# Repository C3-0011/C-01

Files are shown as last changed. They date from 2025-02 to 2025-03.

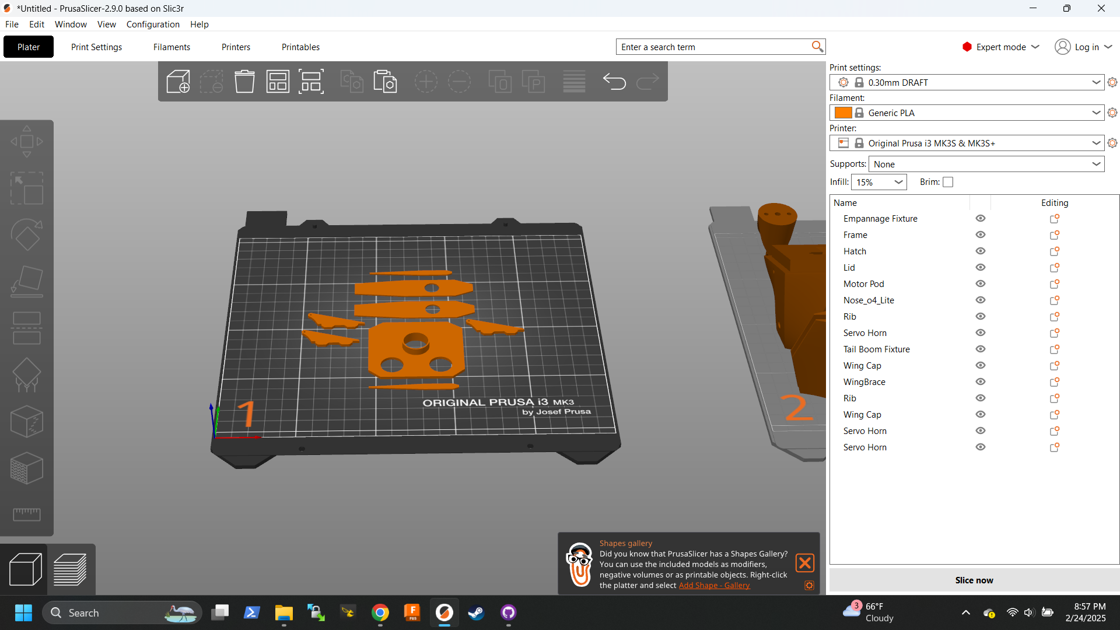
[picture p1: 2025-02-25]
Images/Flat Parts.png

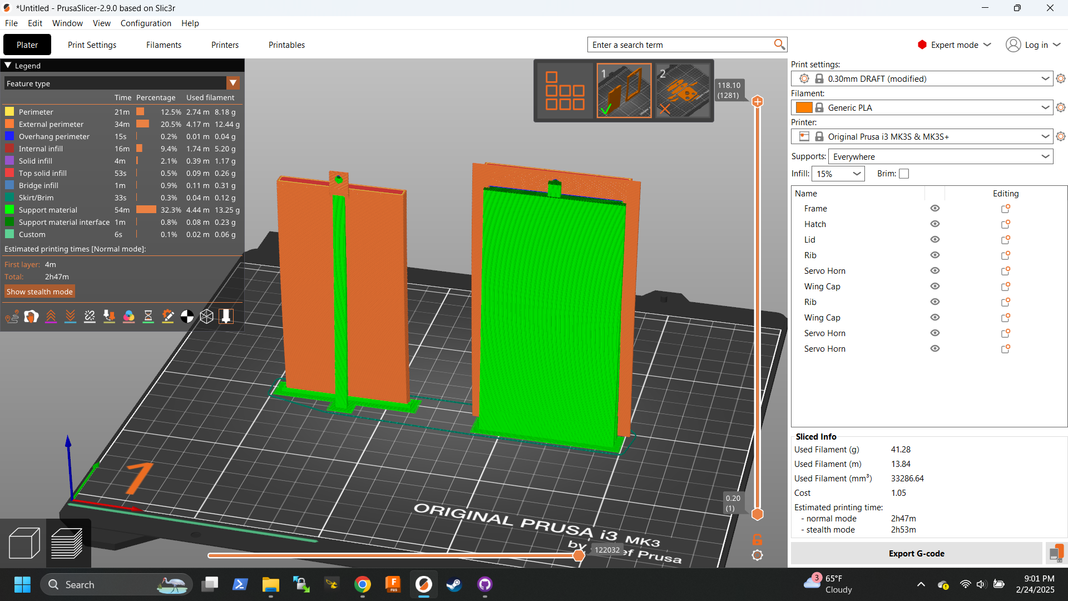
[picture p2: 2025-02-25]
Images/Hatch Parts.png

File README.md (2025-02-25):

# C-01
 T-1 Ranger clone made from foamboard and 3D printed parts

Screenshot (29)

### Parts List:
| Qty | Part | 
| --- | --- |
| 2 | ~2450kv Motors |
| 2 | 5in tri-blade or 6in bi-blade propellers |
| 2 | ~40A PWM Escs |
| 3 | 9g Servo Motors |
| 1 | 360mm X 16mm X 1mm Carbon Fiber Tube |
| 1 | 500mm X 10mm X 1mm Carbon Fiber Tube |
| 1 | 5+ Channel PWM Reciever |
| - | Servo Extensions |
| - | Pushrods |
| - | Video System |
| - | BEC |

## Print Instructions
All of the 3D printed parts are printed in PLA. Lightweight PLA may be suitable but has not been tested.
Print settings are:
- 0.3mm Layer Height
- Cubic 10% Infill
- No supports
Unless stated otherwise.

### Flat Components
Flat Parts
Print the following number of each flat part in the orientation shown above:
| Number | Part |
| --- | --- |
| 2 | Rib |
| 3 | Servo Horn |
| 2 | Wing Cap |
| 1 | Frame |

### Fixtures
Fixtures
Print the following number of each fixture component in the orientation shown above
| Number | Part |
| --- | --- |
| 2 | Wing Brace |
| 2 | Motor Pod |
| 1 | Tail Boom Fixture |
| 1 | Empannage Fixture |

### Hatch Components
Hatch Parts
Print one of each Hatch and Lid components in the orientation shown above. This requires support material on the Hatch component as a minimum, and the Lid also benefits from the stability of adding support. A raft or brim, or slower print speed may help if the Lid component is struggling to adhere to the bed. After printing, install the M3 threaded insert / nut into the 5mm hole in the hatch component using a soldering iron.

### Nose
Nose
Print the nose in the orientation shown above, with the front face flat on the build plate.

If you are using the Analog 22mm nose or the Vista nose, supports should not be required. If you are using the O4 Lite nose then supports are needed, but only to support the USB port. Place a support enforcer such that it covers the "top" part of the usb hole that will need support. You could also enable support everywhere and spend time picking it out, or disable supports completely and file away any sag that may have occured.
o4 Nose

## Cutting Foam Parts
The foam parts are all made from generic Readi-Board from the dollar store. Science fair foam board is not suitable for this model, as it is too dense. The PDF plans are designed to tile and be taped together to form patterns that can be adhered to the stock foamboard with temporary glue, then cut out with a hobby knife. There are 4 sets of patterns, HS (Horizontal Stab.), sides, and tops all have 3 sheets, and the wings pattern has 10 sheets. The wings pattern is made from 2 rows of 5 sheets, with the numbering starting in the top left, going left to right, then repeating on the lower row. The vertical stabilizer pattern is small enough to be printed on one sheet.

I reccomend you calibrate your printer using the 35mm square on the sides3 pdf. To do this, print sides3 at a scale of 100% (never scale to fit) and measure the square with calipers. Then when you print the patterns set the scale equal to: 100 * (35 / your measurement). While cutting out the parts, only cut the very outline for now. The assembly section will give instructions on what to do with the other lines.

 ## Assembly
 The assembly goes much like most Flite Test aircraft, start by building the wings first, then assemble the empennage, then integrate everything as you finish with the fuselage.

 ### Wings
 The wings of the C-01 are inspired by the wings of the FT-3D, I highly encourage you to watch the wings section of the FT-3D build video to see how to score and bevel the lines marked in the wing. Before starting, cut the gray sliver that crosses the leading edge out of the wing, this is where the motor pod will attach. The assembly of the C-01 wings is almost identical to this video, apart from using 3D printed forms to give the wing its shape instead of using foam and the spar. First score the fold lines, and double-bevele the leading edge, and single bevel the aileron on the control surface side. Then glue the Rib component at the root of the wing such that it will force the wing to take the airfoil shape, then do the same with the Wing Cap component at the wingtip. Now follow the gluing and folding procedure in the FT-3D video, but skip the steps where Josh glues down the strips of foam and installs the spar, the C-01 spar goes in at final assembly. Inserting (but not gluing) the motor pod may help ensure the wing takes the proper shape. Make sure to hold, clamp, or press the wing into shape while the hot glue cools. Take the motor pod out if you inserted it. After the wing is cool, attach the motor to the motor pod, then clear any excess glue away from the slot where the motor pod will go. Test fit the motor pod, both pods are identical, but they have a right side up that is flipped for opposite wings. The pod should sit flush against the wing on both sides, and face forward. Note that because the wings are swept, this has the effect of making it look like the motor is pointing towards the wing root before it is attached to the aircraft. If the motor pod is pointing towards the wingtip, it is on backwards. This is also a good time to ensure the motor wires are pointing in a good direction. Once you are sure the motor pod is set up right, insert the motor pod slightly to keep glue from getting on the half-circle where it will touch the wing spar (this is here to help keep the aircraft square during final assembly) then apply a generous amount of glue anywhere the pod will contact the foam. Clean the excess glue off before it cools. Finally glue the Wing Brace component to the root of the wing, such that its rearmost part lies on the hinge axis. This part will bridge the gap between the wing and the fuselage. Repeat these steps for the other wing. When finished, it should look like this: 








### Empennage

Push the Empennage Fixture onto one end of the 16mm carbon fiber tube, pushing it all the way until it is flush. Score and bevel the elevator hinge, beveling on the control surface side, 40mm from the trailing edge of the horizontal stabilizer. Clean the slots in the empennage fixture that the stabilizers will fit into. First push the horizontal stabilizer into place, then the vertical stabilizer. Some CA glue can be used to secure the stabilizers to the fixture, and the fixture to the carbon fiber tube. Cut a space into the vertical stabilizer for the elevator servo, and install a 9g servo there. This is a good time to create and attach the linkages. Use one of the 3D printed servo horns on the elevator. Make sure that the hole in the servo horn is directly above the hinge line when it is glued in place and in the neutral position. You can feed the servo wire through the carbon fiber tube with an extension.

Next install the Tail Boom Fixture onto the other end of the carbon fiber tube. This fixture will sit 63mm from the fuselage end of the tube. Note that this piece is taller than it is wide, and needs to be attached as such. Ensure that it is 63mm from the end of the tube with the "pointy" end facing the empennage, and that it is square with the tail surfaces, then glue it in place with some CA. It should look like this now:



### Final Assembly
First install your video system into your nose of choice. Then take your top and bottom pieces, and remove the paper from one side of them. Next using your calipers score a line 4.4mm from the sides of the top and bottom pieces along the exposed foam. Cut along this line to (but not through) the bottom paper, then remove the piece of foam, these will form a "B" style assembly in the finished fuselage. Next glue the frame piece onto the forward end of the tail boom, making sure it is square (the holes will go up and the "bottom" of the 3d print will be flush with the end of the tube). Then glue the tail boom assembly to the "Bottom" foam piece, applying hot glue under the tail boom fixture and frame pieces. It may be helpful to preform the foam before every step so it takes the bendy shape easily. Next glue the nose piece onto the bottom foam piece, it will sit flush with the bottom as the piece of the nose slots on/over the bottom piece. Next cut the 10mm holes out of the side pieces. Then remove the paper from the inside back section of the side pieces and preform them to the shape they need to take. Add lots of glue along one side of the paper on the edge of the bottom piece, and the side of the nose, frame, and tail boom fixture pieces, and push the corresponding side foam piece onto the bottom piece, forming both the side and bottom to take eachother's shape as the glue cools, then repeat this on the other side. Next tack the 10mm carbon tube in place inside the spar holes, centered over the airframe. Next grab one wing. Test fit the wing, ensuring that the spar does not snag as it is inserted. You should feel how it locates onto the half-circle on the end of the motor pod. Once you are sure the fit is good, apply a generous amount of hot glue onto anywhere the wing will contact the fuselage, and push it firmly against the fuselage. While the glue dries, make sure the wing is parallel to the tail boom. The C-01 has a designed angle of incidence of zero, and the wings are coplanar with the tail boom to make alignment by eye easier. Repeat this with the other wing. Once both wings are installed, install the aileron servos forward of the "Frame" piece. This will involve cutting a hole for them in the fuselage sides underneath the wings. Then install the servo horns and linkages. Then install the reciever behind the wing spar, and put together and test the electrical system. Once the top is on it will be very difficult to access this area, so ensure everything is working properly before moving forward. When you are ready to put the top on, add glue everywhere it will contact the fuselage, and press it into place. Next cut a 58mmx117mm hole in the top plate, with the front edge of the hole 13mm from where the top plate meets the nose piece. Glue the Hatch piece into this hole, and add fuzzy velcro to the space beneath it to secure a battery.

I will add photos here when I rebuild my fuselage this week.

## Misc

The C-01 is designed to be flown with the motors on seperate channels for differential thrust, and the aileron servos on independent channels so that flaperons can be configured. Give the control surfaces roughly 30 degrees of deflection, and I'd reccomend 20-30 percent expo. I fly my C-01 with a 3s 2200, however with the the speced motors, props, and escs, it should be capable of 4s without burning any electronics. Balance the C-01 roughly over the spar.

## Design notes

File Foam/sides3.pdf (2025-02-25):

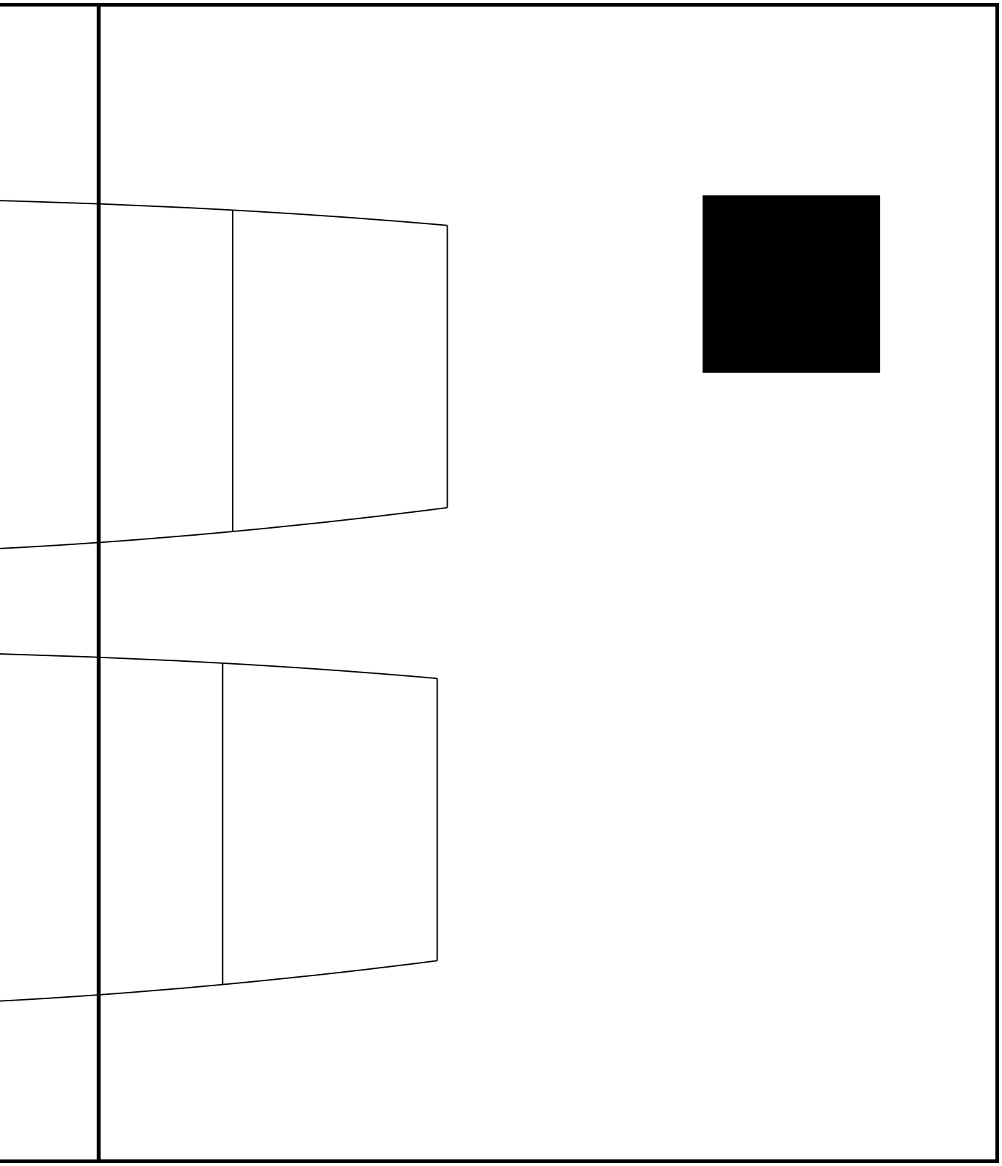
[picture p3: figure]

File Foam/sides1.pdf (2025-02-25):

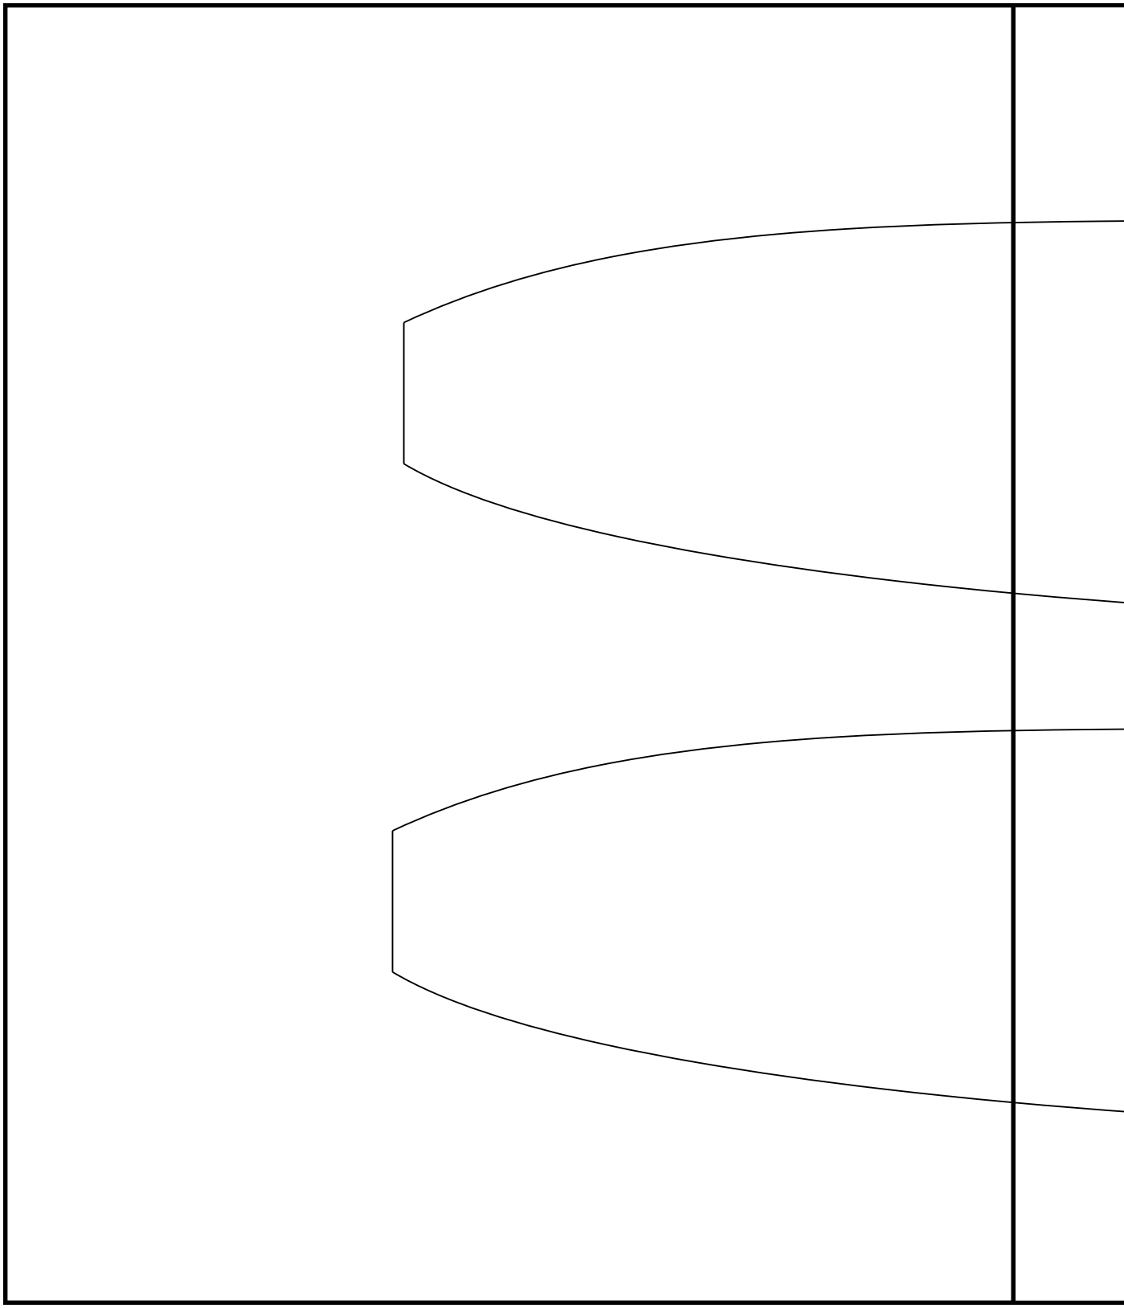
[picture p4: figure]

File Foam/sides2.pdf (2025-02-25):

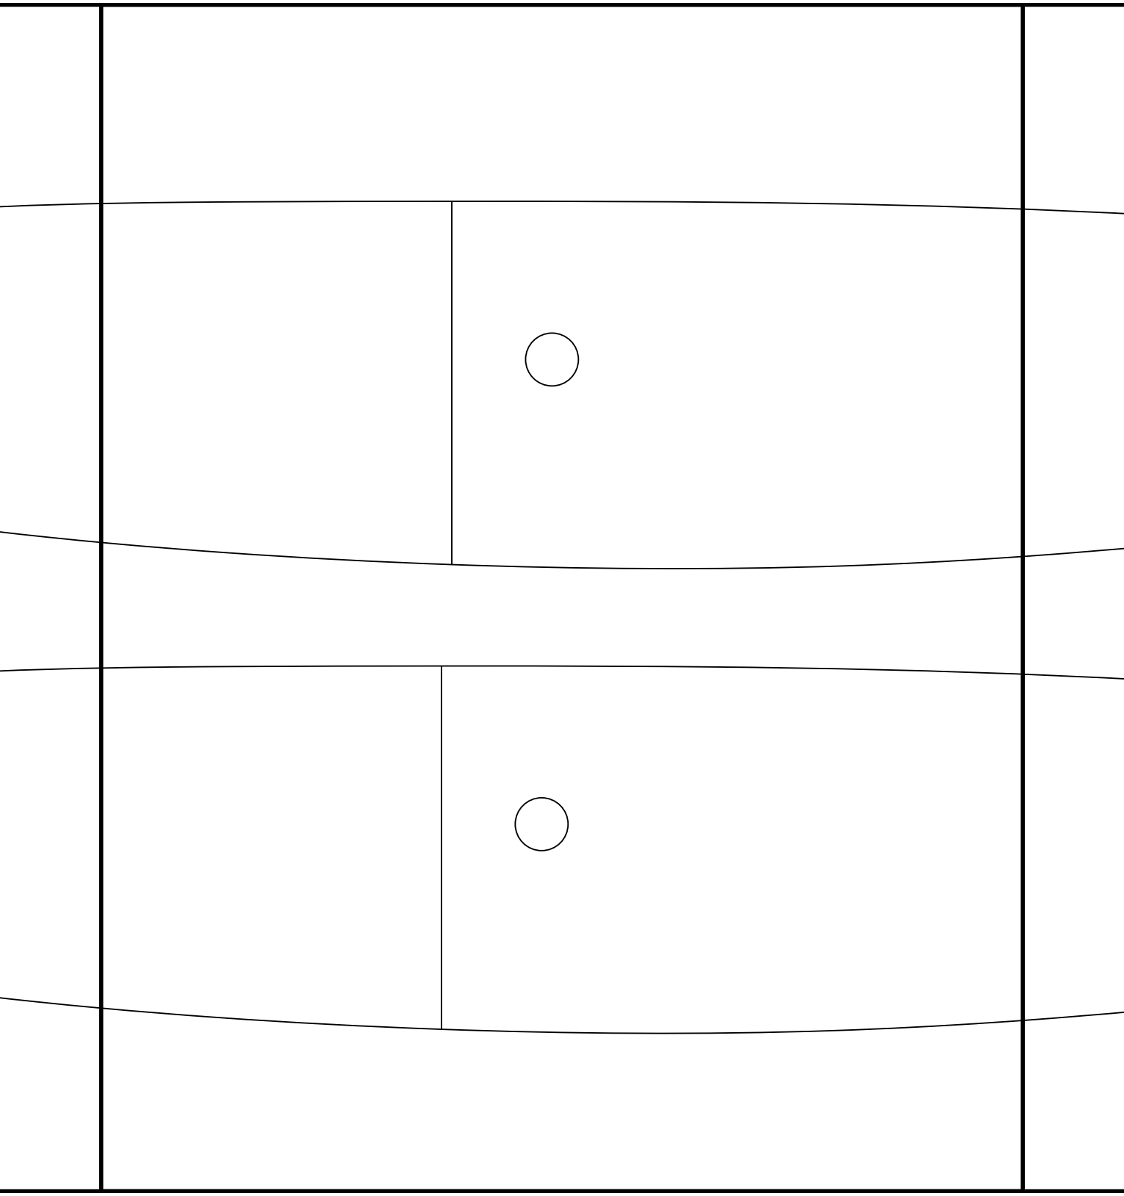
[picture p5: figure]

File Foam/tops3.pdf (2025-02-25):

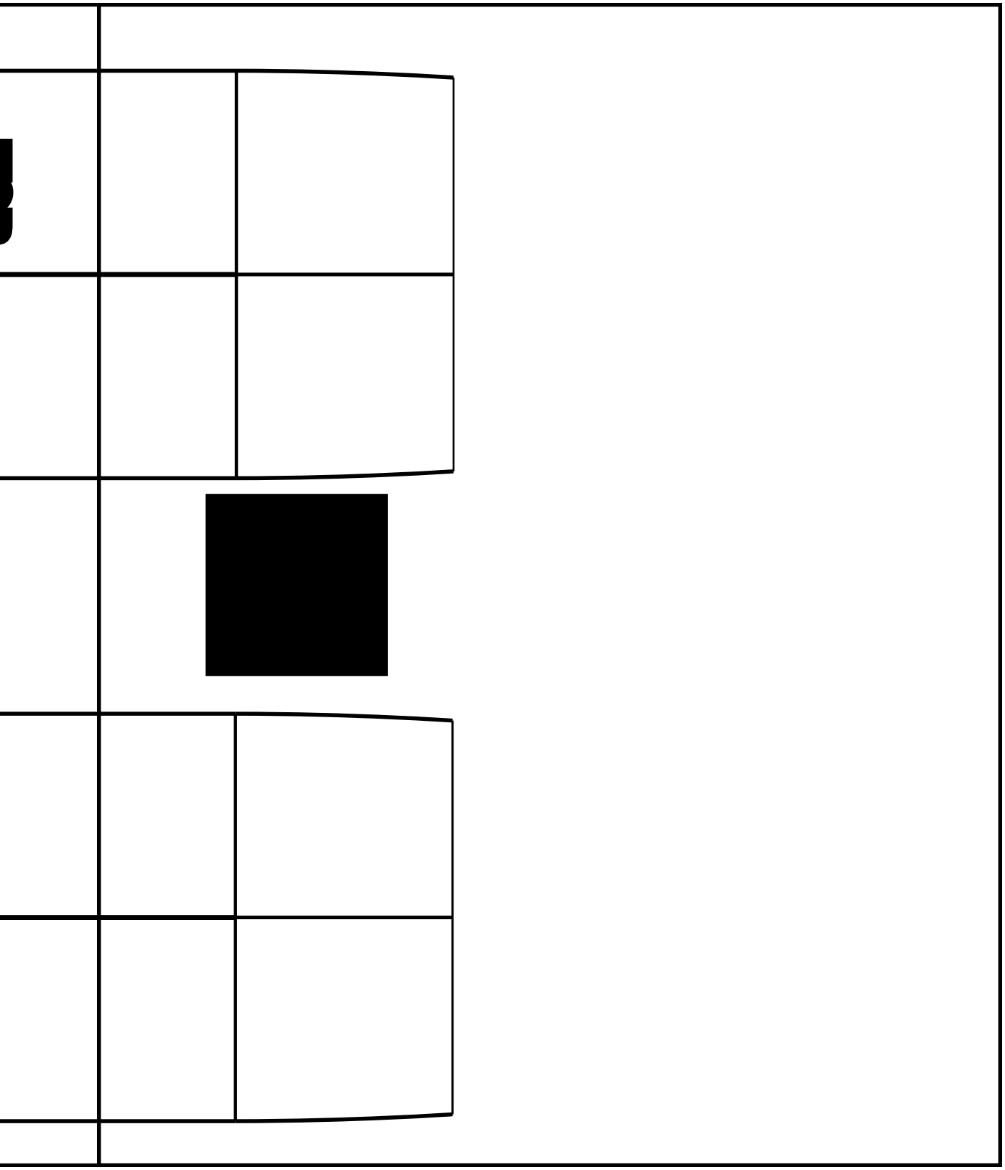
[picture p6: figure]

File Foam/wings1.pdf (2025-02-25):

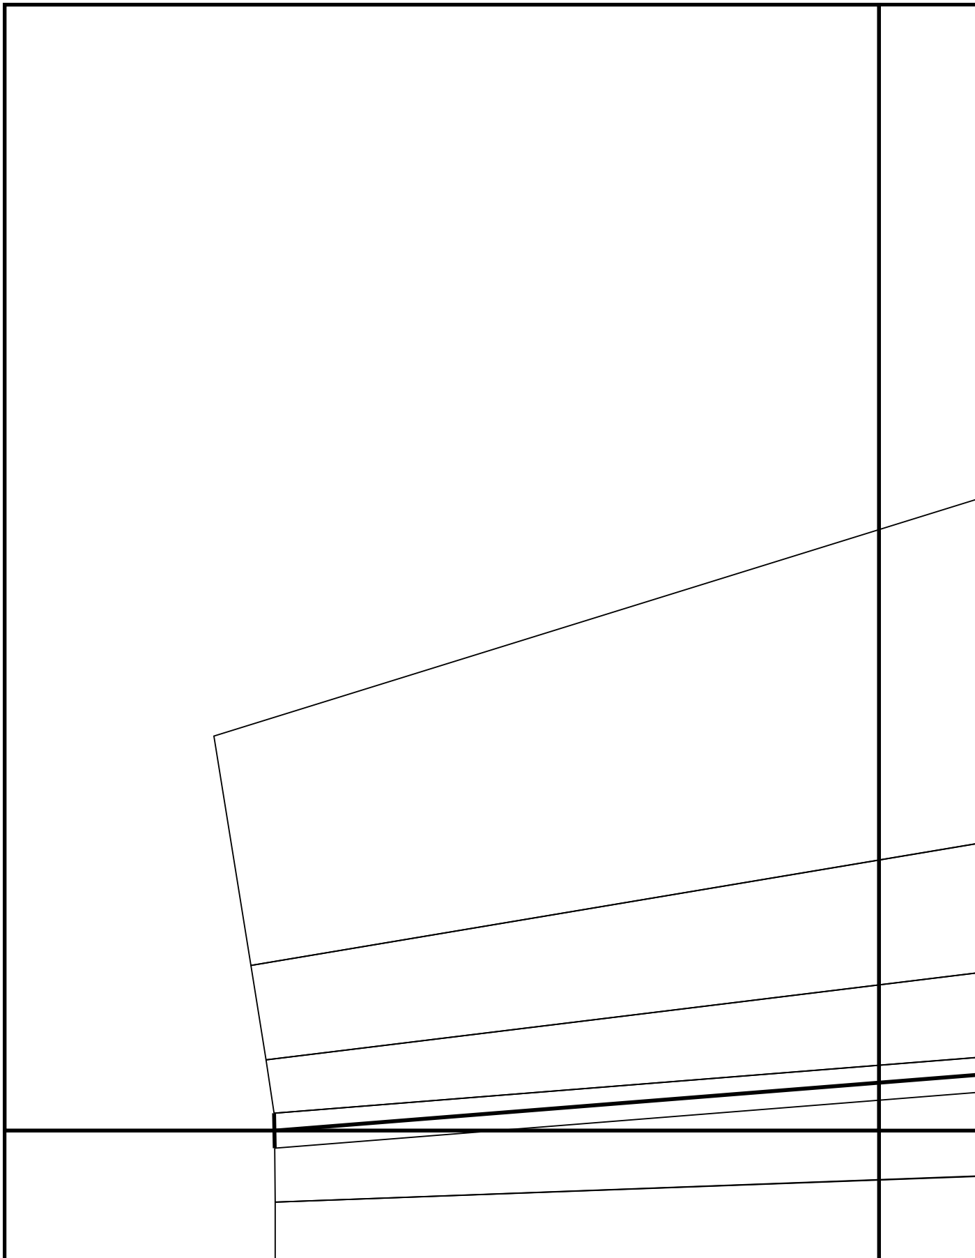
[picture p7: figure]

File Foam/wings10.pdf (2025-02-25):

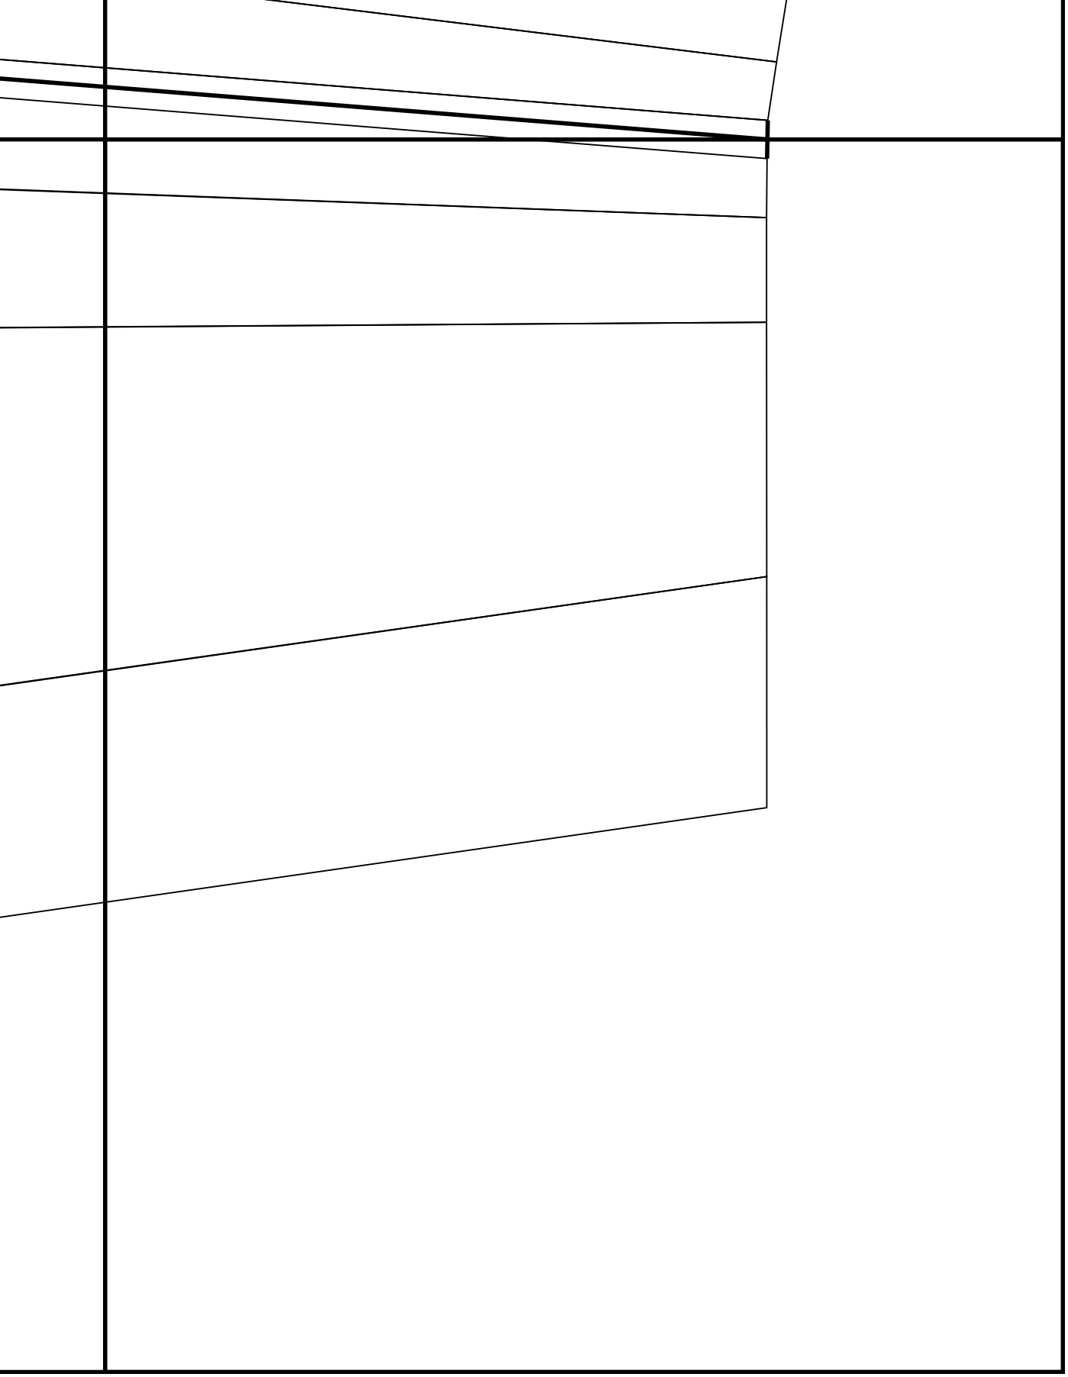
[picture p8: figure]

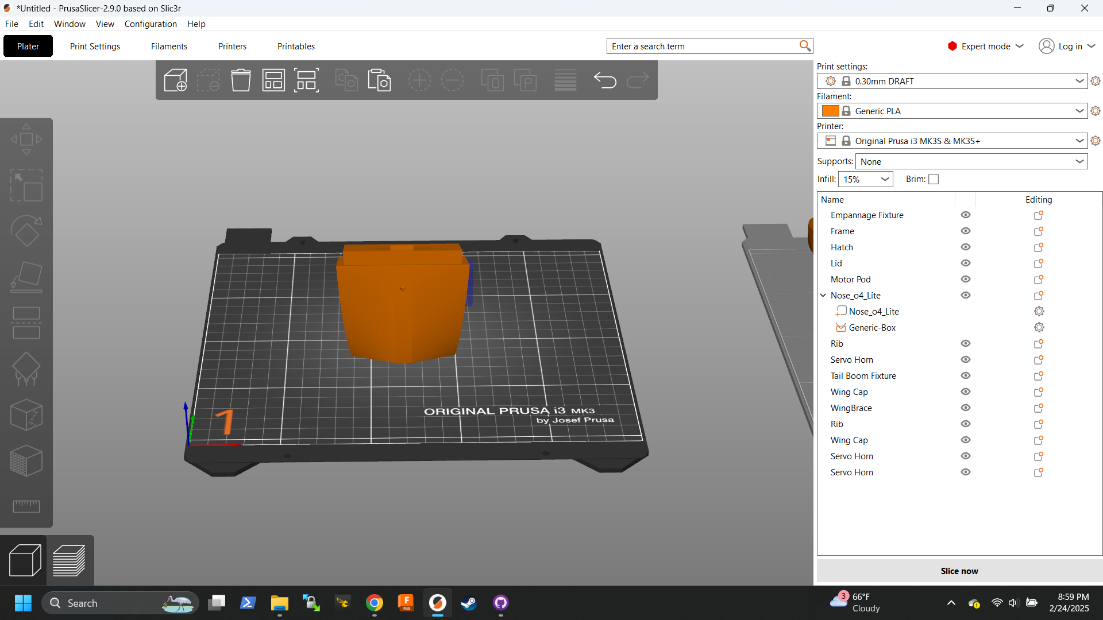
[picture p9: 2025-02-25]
Images/Nose.png

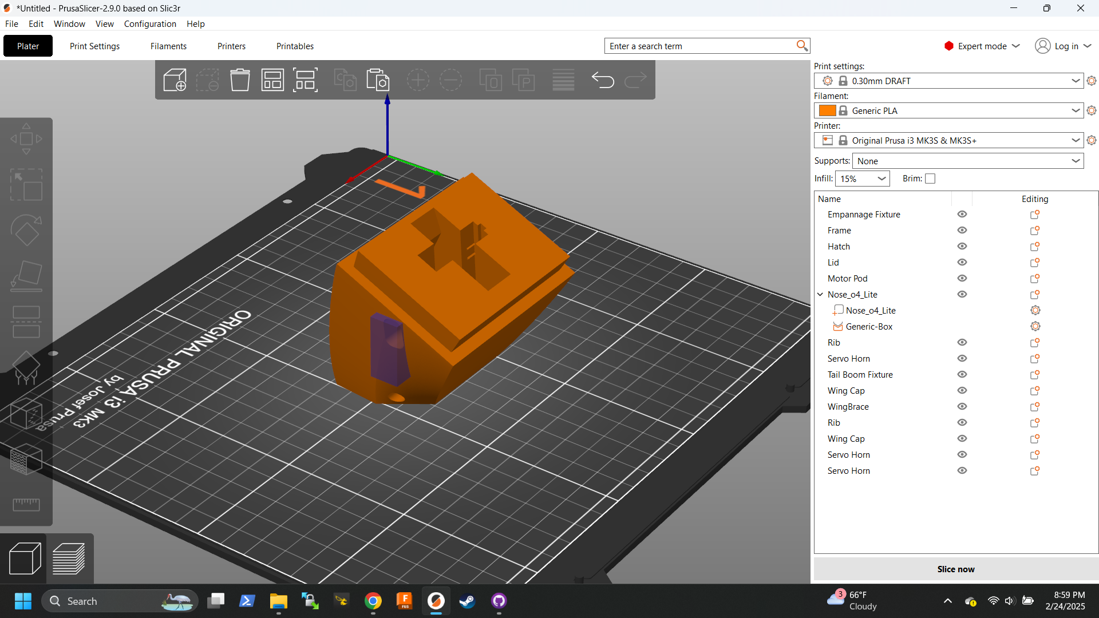
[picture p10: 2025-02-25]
Images/o4 Nose.png

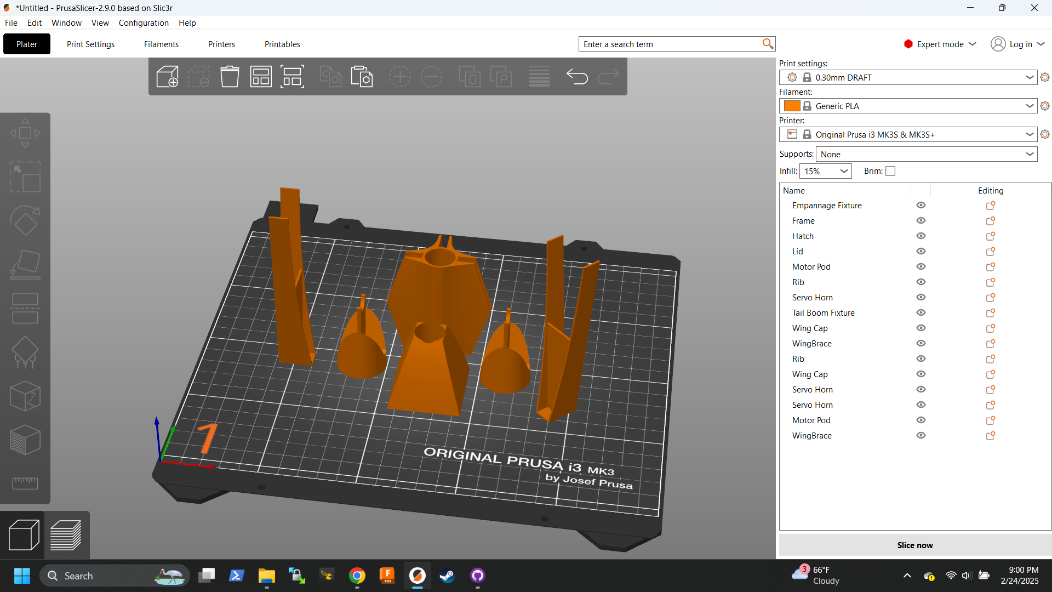
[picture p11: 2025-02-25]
Images/Fixtures.png

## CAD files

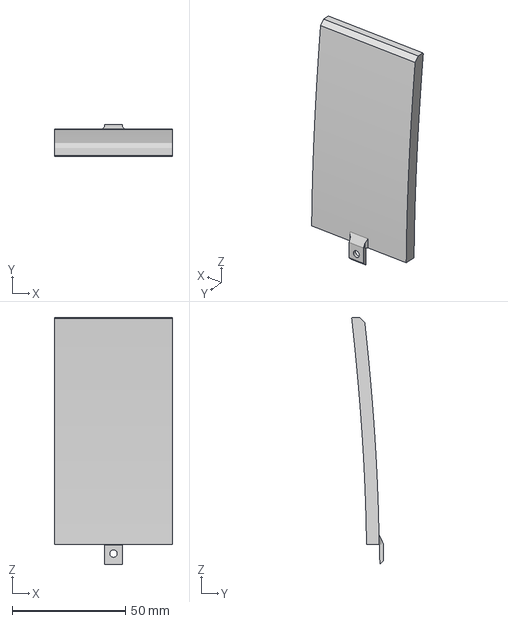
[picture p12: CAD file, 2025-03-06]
PLA/Lid.3mf
52.4 x 14.0 x 109.3 mm

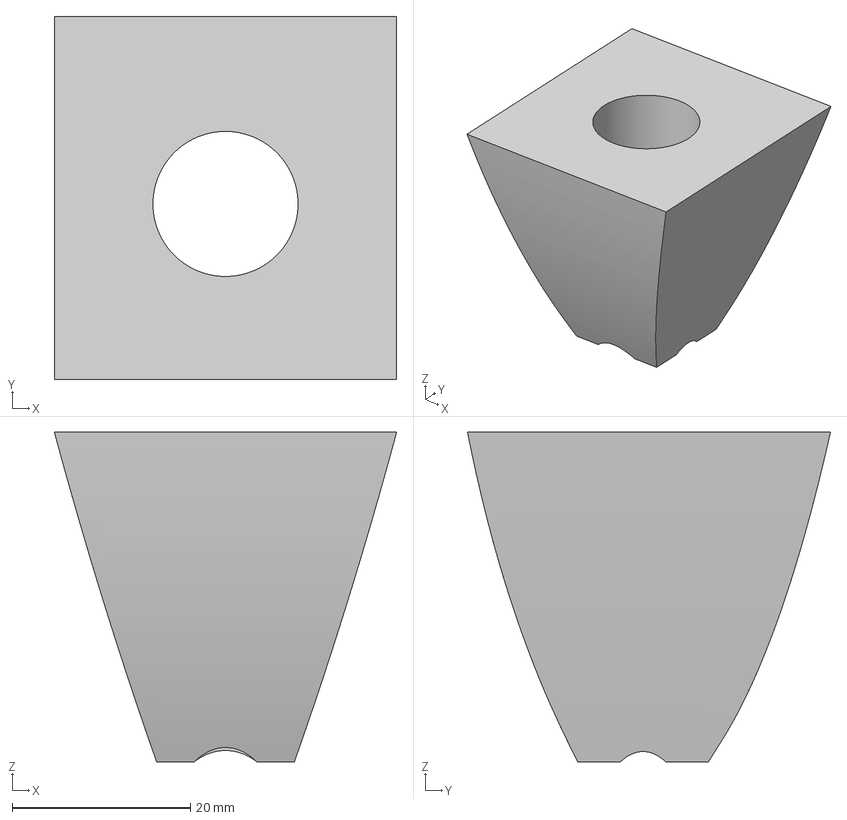
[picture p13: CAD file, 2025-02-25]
PLA/Tail Boom Fixture.3mf
38.4 x 40.8 x 37.0 mm

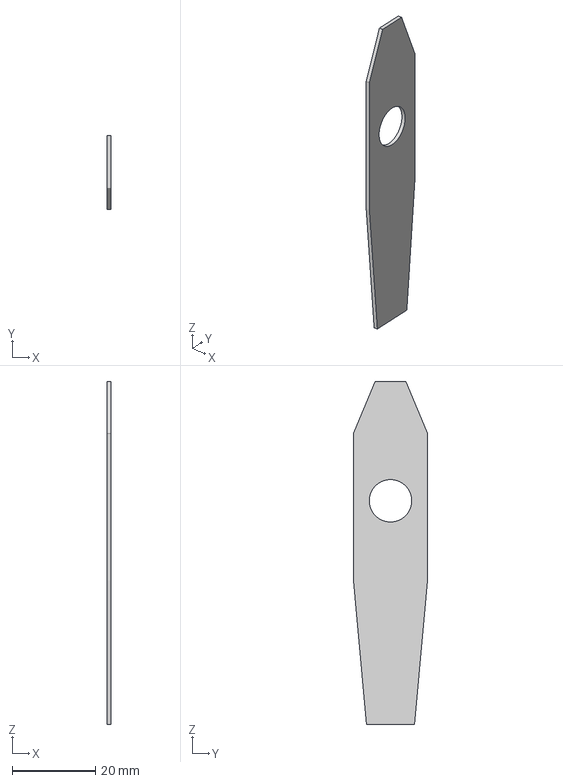
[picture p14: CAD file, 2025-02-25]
PLA/Rib.3mf
1.00 x 17.8 x 82.6 mm

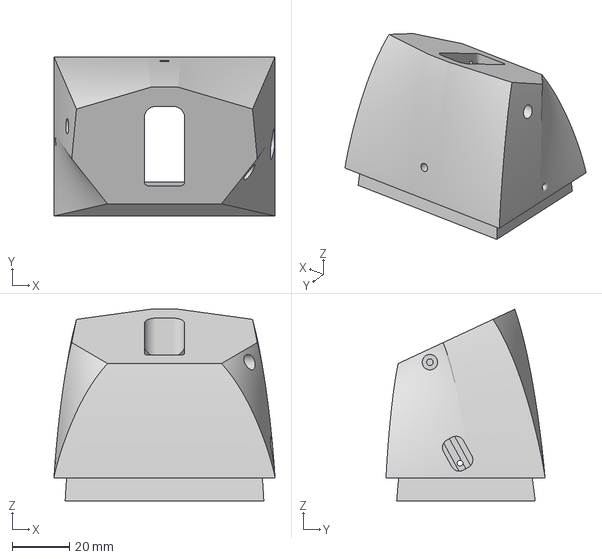
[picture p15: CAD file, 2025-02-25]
PLA/Nose_o4_Lite.3mf
77.3 x 55.6 x 67.0 mm

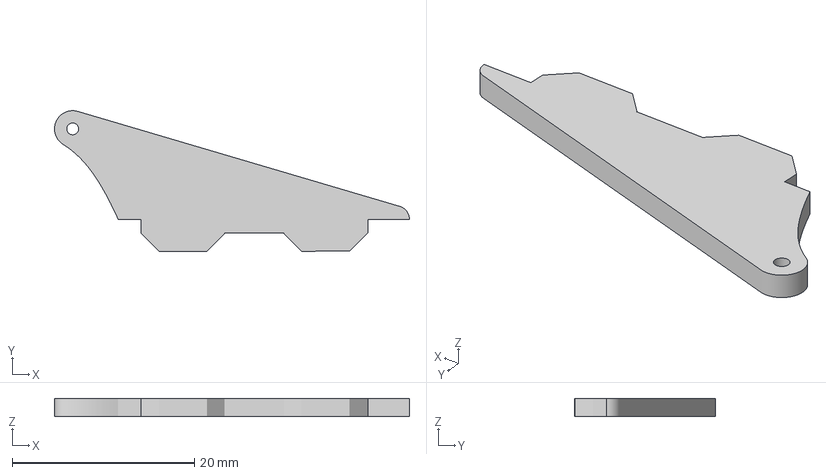
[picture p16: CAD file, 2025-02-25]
PLA/Servo Horn.3mf
39.0 x 15.5 x 2.00 mm

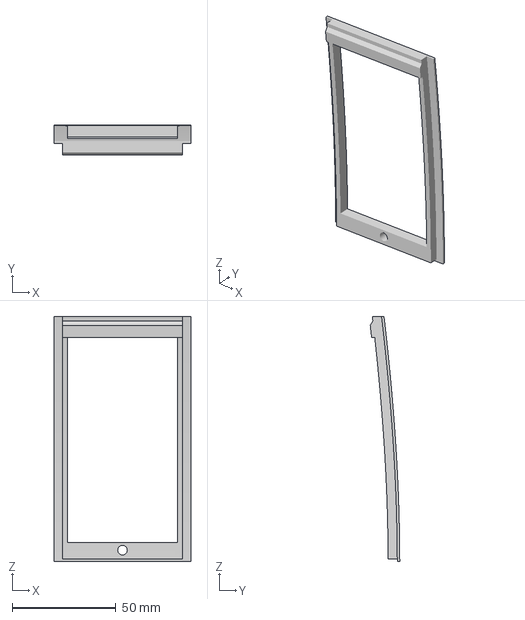
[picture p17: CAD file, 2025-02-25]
PLA/Hatch.3mf
66.0 x 14.2 x 118.2 mm

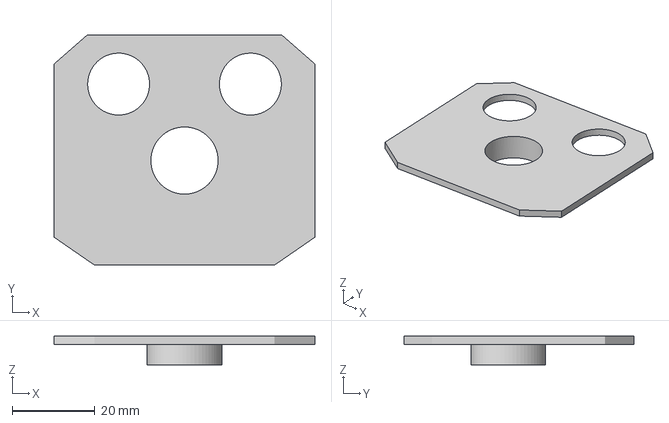
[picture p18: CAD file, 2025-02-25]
PLA/Frame.3mf
63.2 x 55.7 x 7.00 mm

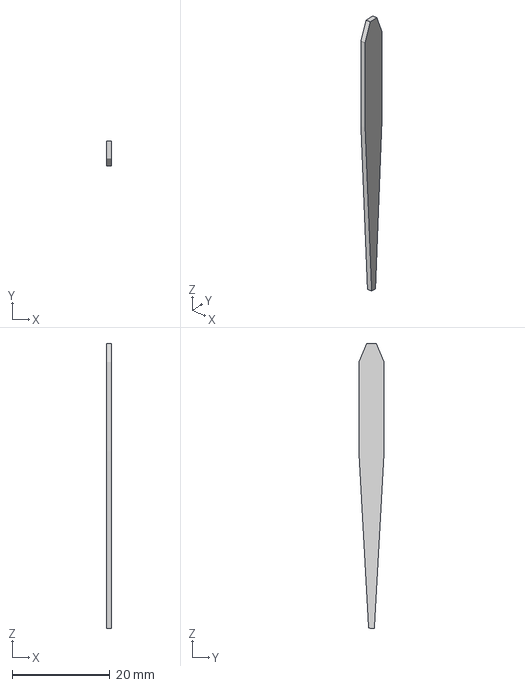
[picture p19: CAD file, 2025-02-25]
PLA/Wing Cap.3mf
1.00 x 5.18 x 58.4 mm

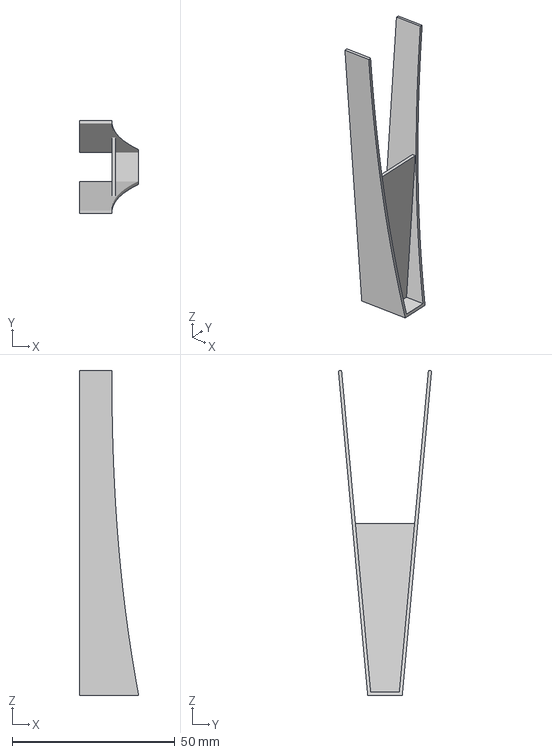
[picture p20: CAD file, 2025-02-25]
PLA/WingBrace.3mf
18.3 x 28.6 x 99.8 mm

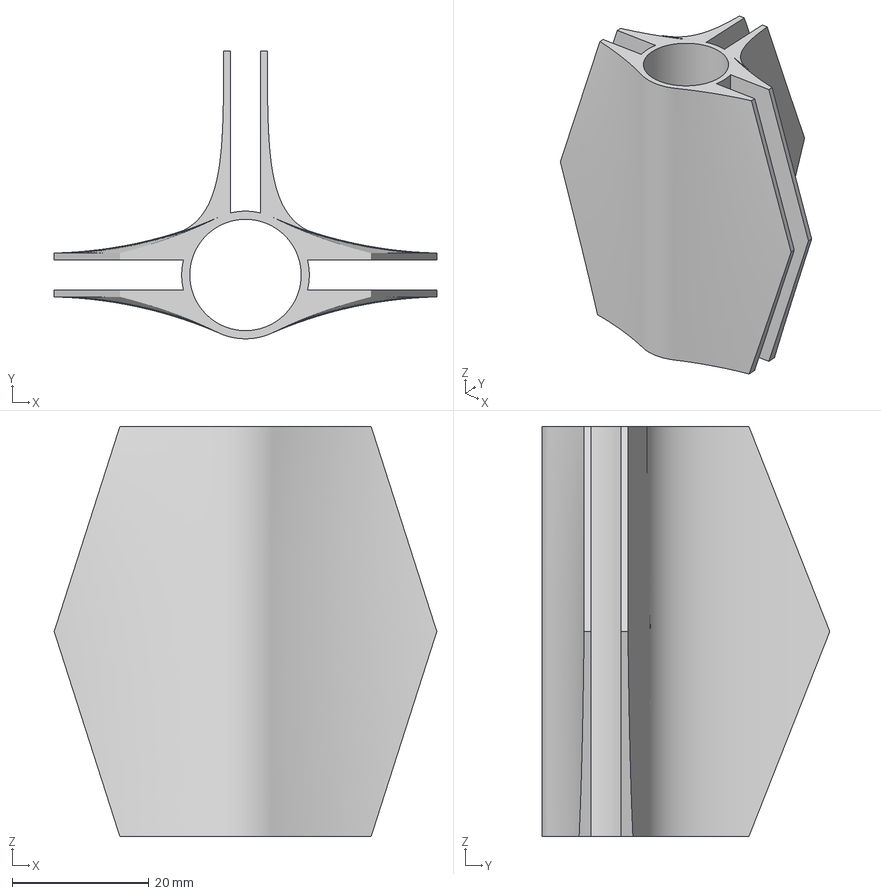
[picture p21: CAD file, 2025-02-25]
PLA/Empannage Fixture.3mf
56.0 x 42.1 x 60.0 mm

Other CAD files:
C-01_Fusion.f3d

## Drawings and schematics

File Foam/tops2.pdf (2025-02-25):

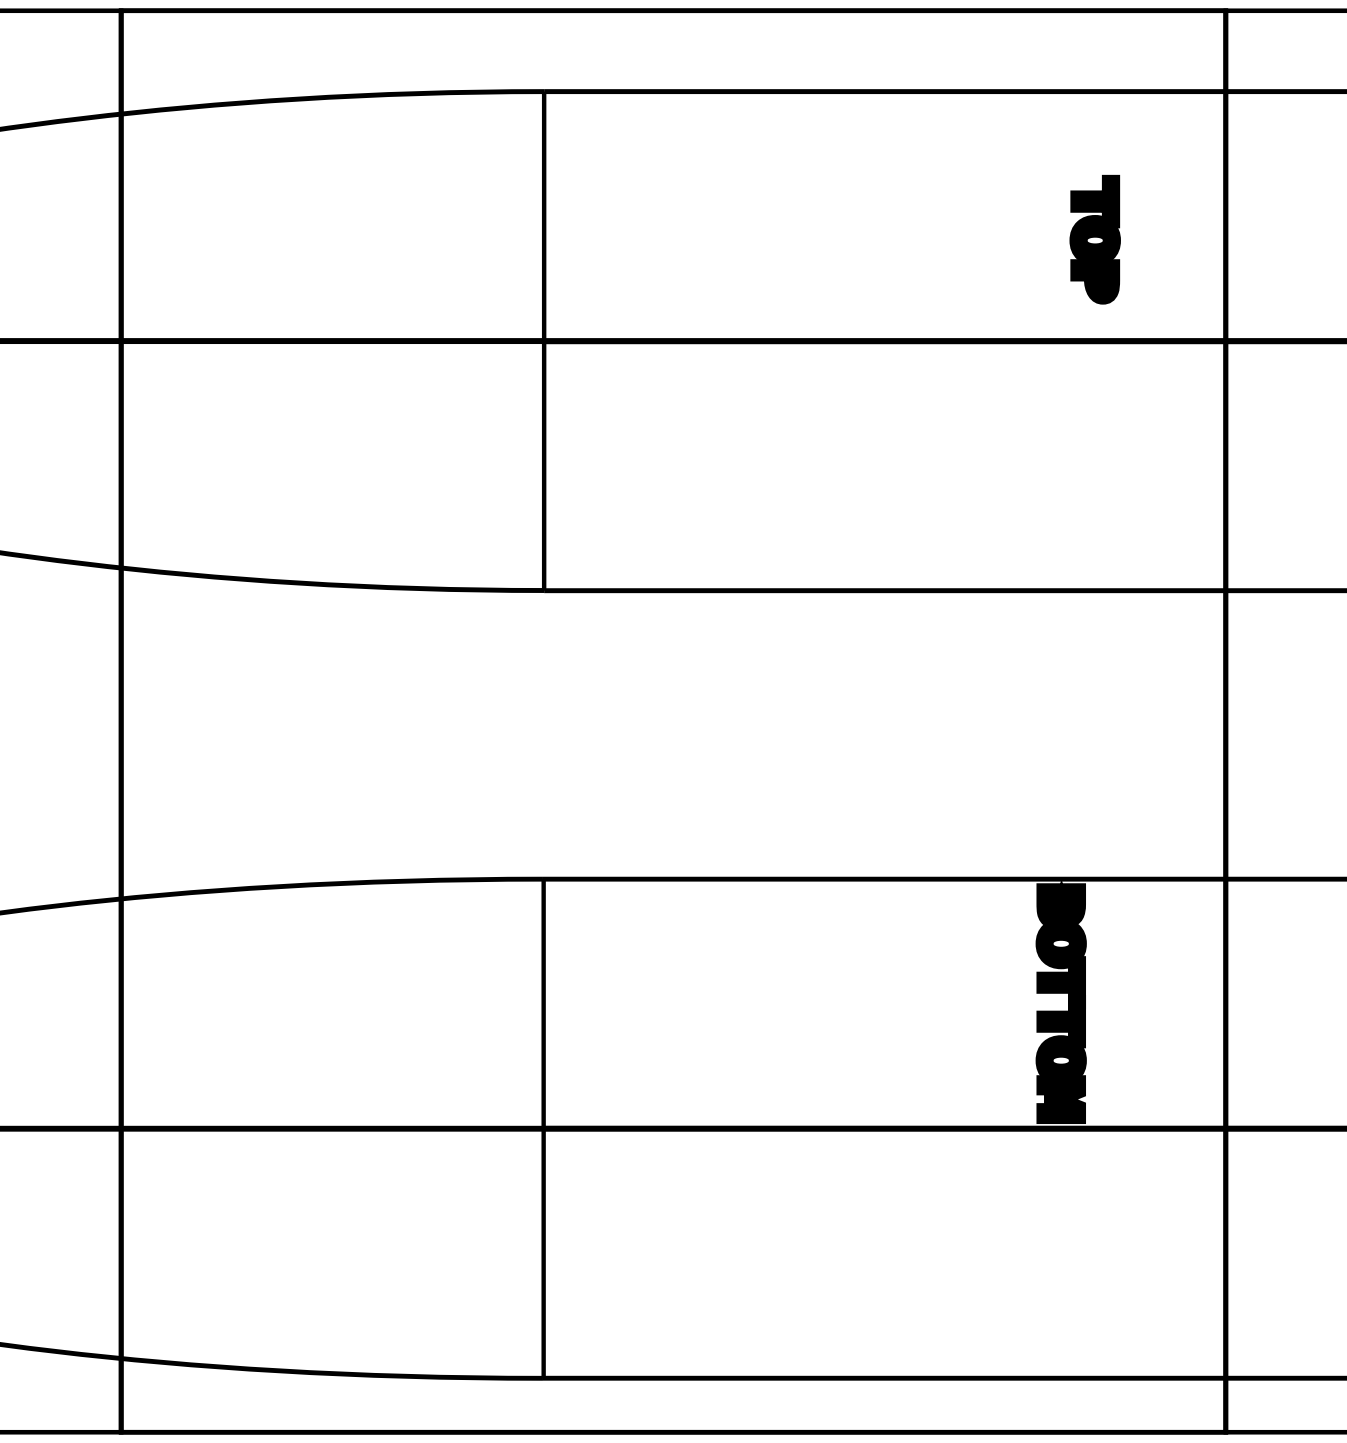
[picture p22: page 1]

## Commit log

2025-02-25 Added Existing Parts
    [Empannage Fixture.3mf, Frame.3mf, Hatch.3mf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]
2025-02-25 Added 3D print orientation images
    [WingBrace L.3mf, WingBrace R.3mf, WingBrace.3mf]
2025-02-25 Uploaded fusion archive file
    [C-01_Fusion.f3d]
2025-03-06 Made tab on lid thicker
    [C-01_Fusion.f3d, Lid.3mf]
